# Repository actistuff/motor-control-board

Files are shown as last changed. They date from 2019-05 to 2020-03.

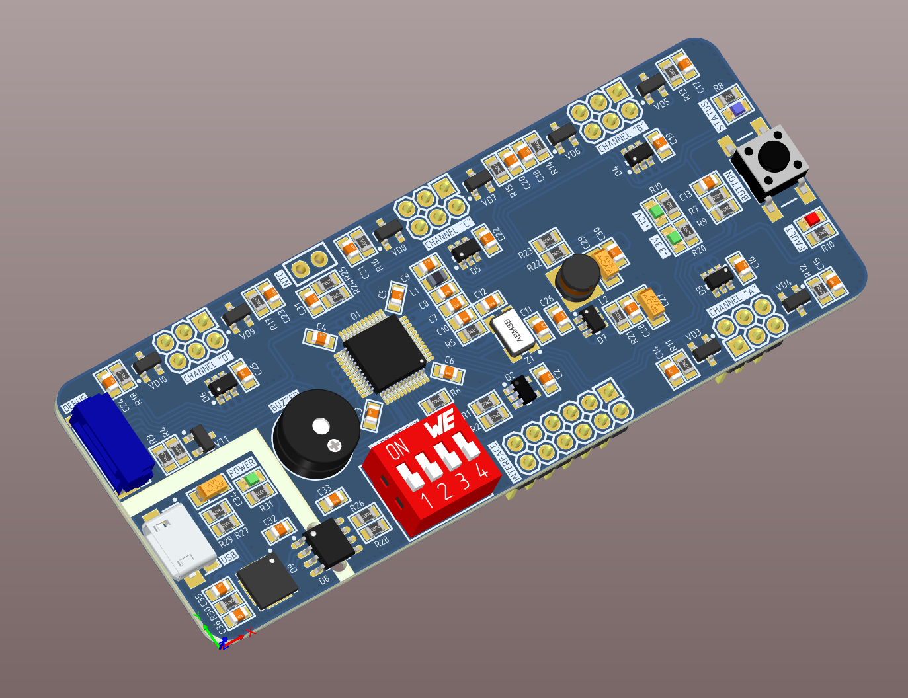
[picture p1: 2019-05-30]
Hardware/Mechanical/3D view. Part 1.PNG

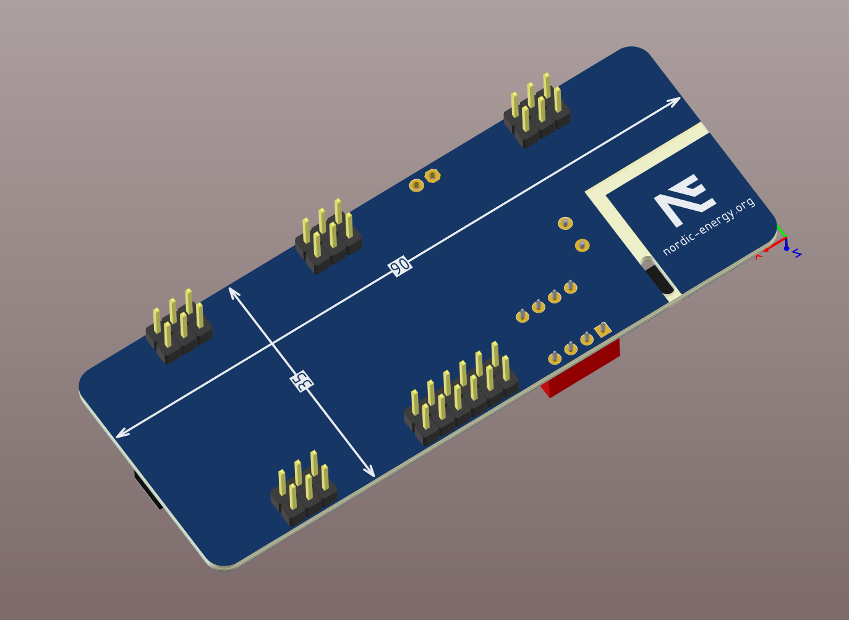
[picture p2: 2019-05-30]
Hardware/Mechanical/3D view. Part 2.PNG

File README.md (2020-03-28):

# Модуль управления силовым преобразователем

Проект создан для упрощения процесса разработки и создания прототипов силовых преобразователей энергии: инверторов напряжения, MPPT контроллеров, сварочных истоников тока, корректоров коэффициента мощности и т.д. Основой проекта является аппаратный модуль на базе специализированного (motor control) микроконтроллера STM32F334C8T6, адаптированный под прототипирование различных топологий преобразователей энергии. 

Плата управления

Особенно полезен модуль *MotorControlBoard* будет тем, кто только начинает изучать силовую электронику, так как его применение в процессе прототипирования позволит вам избавиться от большинства аппаратных проблем и упростить устройство. Важной частью проекта является наличие примеров *(Example)* кода для базовых топологий преобразователей и элементов системы управления.

# Технические характеристики

* Микроконтроллер: *STM32F334C8T6*
* Ядро контроллера: *Cortex-M4*
* Частота: *72 МГц*
* Наличие HRPWM: *да*
* Наличие FPU: *да*
* Внешняя EEPROM: *2 Кбит*
* Количество каналов: *4 полумоста*
* Напряжение питания: *5...18В*
* Ток потребления: *не более 0.07А*
* Температурный диапазон: *-20...+85°С*

# Структура проекта

* Firmware
    * Documents
    * Examples
    * Library

>

* Hardware
    * Documents
    * Manufacture
    * AltiumProject
    * Mechanical

# Назначение выводов

Модуль содержит 4 канала для управления полумостом, каждый из которых выведен на разъем PLS-6 и содержит в себе 2 канала HRPWM, 2 канала АЦП, вход сигнала ошибки и землю. Так же имеется основной вход для подачи питания, сигналов синхронизации и дополнительные I/O с программируемым функционалом.

Pinout

# Используемые инструменты

* [Altium Designer](https://www.altium.com/altium-designer/ "Официальный сайт CAD")
* [Visual Studio 2019](https://visualstudio.microsoft.com/ru/vs/ "Официальный сайт IDE")
* [VisualGDB](https://visualgdb.com/download/ "Официальный сайт плагина")
* [PVS-Studio](https://www.viva64.com/ru/pvs-studio/ "Официальный сайт")

# Лицензирование

Все исходные материалы для проекта распространяются по лицензии [MIT](./LICENSE "Описание лицензии"). Вы можете использовать проект в любом виде, в том числе и для коммерческой деятельности, но стоит помнить, что автор проекта не дает никаких гарантий на работоспособность устройства или частей проекта, а так же не несет никакой ответственности по искам или за нанесенный ущерб.

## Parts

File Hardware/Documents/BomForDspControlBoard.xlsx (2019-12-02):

Designator | Value | PartNumber | Manufacturer | Quantity | Comment | HelpURL
C1, C16, C17 | 1μF | CL10B105KO8NNNC | Samsung | 3 | Ceramic capacitor, 1μF, X7R, ±10%, 16V, 0603, -55...+125°C | https://www.digikey.com/product-detail/en/samsung-electro-mechanics/CL10B105KO8NNNC/1276-1019-1-ND/3889105
C2, C3, C4, C5, C6, C7, C8, C9, C34, C35, C39 | 10μF | CL10B106MQ8NRNC | Samsung | 11 | Ceramic capacitor, 10μF, X7R, ±10%, 6.3V, 0603, -55...+125°C | https://www.digikey.com/product-detail/en/samsung-electro-mechanics/CL10B106MQ8NRNC/1276-1948-1-ND/3890034
C10, C11, C12, C18, C21, C30, C31, C32, C33, C36, C40 | 0.1μF | CL10B104KB8NNNC | Samsung | 11 | Ceramic capacitor, 0.1μF, X7R, ±10%, 50V, 0603, -55...+125°C | https://www.digikey.com/product-detail/en/samsung-electro-mechanics/CL10B104KB8NNNC/1276-1000-1-ND/3889086
C15, C22, C23, C24, C25, C26, C27, C28, C29 | 0.01μF | CL10B103KB8NNNC | Samsung | 9 | Ceramic capacitor, 0.01μF, X7R, ±10%, 50V, 0603, -55...+125°C | https://www.digikey.com/product-detail/en/samsung-electro-mechanics/CL10B103KB8NNNC/1276-1009-1-ND/3889095
C19, C20 | 12pF | CL10C120JB8NNNC | Samsung | 2 | Ceramic capacitor, 12pF, NPO, ±10%, 50V, 0603, -55...+125°C | https://www.digikey.com/product-detail/en/samsung-electro-mechanics/CL10C120JB8NNNC/1276-1254-1-ND/3889340
C37 | 2.7pF | CL10C2R7BB8NNNC | Samsung | 1 | Ceramic capacitor, 2.7pF, NPO, ±10%, 50V, 0603, -55...+125°C | https://www.digikey.com/product-detail/en/samsung-electro-mechanics/CL10C2R7BB8NNNC/1276-1240-1-ND/3889326
C38 | 4.7pF | CL10C4R7CB8NNNC | Samsung | 1 | Ceramic capacitor, 4.7pF, NPO, ±10%, 50V, 0603, -55...+125°C | https://www.digikey.com/product-detail/en/samsung-electro-mechanics/CL10C4R7CB8NNNC/1276-1282-1-ND/3889368
D1 |  | TCAN334DCNR | Texas Instruments | 1 | IC CAN transceiver, 1Mbps, Half-duplex, 3...3.6V, -40...+125°C, SOT23-8 | https://www.digikey.com/product-detail/en/texas-instruments/TCAN334DCNR/296-47830-1-ND/8133179
D2, D3 |  | AP3429AKTTR-G1 | Diodes Incorporated | 2 | DC/DC buck converter, input 2.7...5.5V, 1MHz, output 0.6...5V, 2A, -40...+85°C, SOT23-6 | https://www.digikey.com/product-detail/en/diodes-incorporated/AP3429AKTTR-G1/AP3429AKTTR-G1DICT-ND/5359842
D4 |  | TLV70033DDCR | Texas Instruments | 1 | Linear voltage regulator, input 5.5V, 0.25V, output 3.3V, 200 mA, -40...+85°C, SOT-23-5 | https://www.digikey.com/product-detail/en/texas-instruments/TLV70033DDCR/296-27937-1-ND/2440840
D5 |  | STM32F334C8T6 | STMicroelectronics | 1 | IC microcontroller, 32-Bit, Cortex-M4, 72MHz, 64KB, 12KB, 2...3.6V, -40...+85°C, 48-LQFP | https://www.digikey.com/products/en?keywords=STM32F334C8T6
D6, D8, D9, D11, D12, D13, D14 |  | SN74LVC2G17DCKR | Texas Instruments | 7 | IC logic buffer, 1.65...5.5V, -40...+125°C, SC-70-6 | https://www.digikey.com/product-detail/en/texas-instruments/SN74LVC2G17DCKR/296-13013-1-ND/479736
D7 |  | 24AA01T-I/OT | Microchip Technology | 1 | IC memory, EEPROM, 1KB (128x8), 400 kHz, I2C, 1.7...5.5V, -40...+85°C, SOT-23-5 | https://www.digikey.com/product-detail/en/microchip-technology/24AA01T-I-OT/24AA01T-I-OTCT-ND/857670
D10 |  | 5M80ZE64I5N | Intel | 1 | IC CPLD logic, MAX V, 100MHz, 80LE, 1.71...1.89V, -40...+100°C, 64-EQFP | https://www.digikey.com/product-detail/en/intel/5M80ZE64I5N/544-2817-ND/2660734
D15 |  | ESP32-PICO-D4 | Espressif Systems | 1 | IC RF transceiver, 802.11b/g/n + Bluetooth v4.2, 2.4GHz, 32-Bit, Xtensa LX6, 4Mb, 520KB, 2.7...3.6V, -40...+85°C, 48-LGA | https://www.digikey.com/product-detail/en/espressif-systems/ESP32-PICO-D4/1904-1029-1-ND/9381738
L1, L2 | 4.7μH | SRP2510A-4R7M | Bourns | 2 | Fixed inductor, 4.7μH, ±20%, SRP2510A, 1.36A, -40...+125°C | https://www.digikey.com/product-detail/en/bourns-inc/SRP2510A-4R7M/SRP2510A-4R7MCT-ND/7354840
L3 | 10μH | LQM18FN100M00D | Murata Electronics | 1 | Fixed inductor, 10μH, ±20%, 0603, 50mA, -55...+125°C | https://www.digikey.com/product-detail/en/murata-electronics-north-america/LQM18FN100M00D/490-4025-1-ND/1016285
L4 | 1.6nH | CW161009A-1N6D | Bourns | 1 | Fixed inductor, 1.6nH, ±20%, 0603, 700mA, -40...+125°C | https://www.digikey.com/product-detail/en/bourns-inc/CW161009A-1N6D/CW161009A-1N6DCT-ND/9826842
R1 | 120R | RC0603JR-07120RL | Yageo | 1 | Resistor film, 120R, ±5%, 0603, 0.1W, -55...+125°C | https://www.digikey.com/product-detail/en/yageo/RC0603JR-07120RL/311-120GRCT-ND/729653
R2, R4 | 10k | RC0603FR-0710KL | Yageo | 2 | Resistor film, 10k, ±1%, 0603, 0.1W, -55...+125°C | https://www.digikey.com/product-detail/en/yageo/RC0603FR-0710KL/311-10.0KHRCT-ND/729827
R3 | 2k2 | RC0603FR-072K2L | Yageo | 1 | Resistor film, 2k2, ±1%, 0603, 0.1W, -55...+125°C | https://www.digikey.com/product-detail/en/yageo/RC0603FR-072K2L/311-2.20KHRCT-ND/729963
R5 | 4k99 | RC0603FR-074K99L | Yageo | 1 | Resistor film, 4k99, ±1%, 0603, 0.1W, -55...+125°C | https://www.digikey.com/product-detail/en/yageo/RC0603FR-074K99L/311-4.99KHRCT-ND/730166
R6, R7, R35, R36, R38 | 10k | RC0603JR-0710KL | Yageo | 5 | Resistor film, 10k, ±5%, 0603, 0.1W, -55...+125°C | https://www.digikey.com/product-detail/en/yageo/RC0603JR-0710KL/311-10KGRCT-ND/729647
R8, R9, R12, R13, R14, R15, R16, R17, R18, R19, R20, R21, R22, R23, R24, R25, R26, R27, R28, R29, R30, R31, R32, R33, R34 | 100R | RC0603JR-07100RL | Yageo | 25 | Resistor film, 100R, ±5%, 0603, 0.1W, -55...+125°C | https://www.digikey.com/product-detail/en/yageo/RC0603JR-07100RL/311-100GRCT-ND/729644
R10, R11 | 4k7 | RC0603JR-074K7L | Yageo | 2 | Resistor film, 4k7, ±5%, 0603, 0.1W, -55...+125°C | https://www.digikey.com/product-detail/en/yageo/RC0603JR-074K7L/311-4.7KGRCT-ND/729732
R37 | 1k | RC0603JR-071KL | Yageo | 1 | Resistor film, 1k, ±5%, 0603, 0.1W, -55...+125°C | https://www.digikey.com/product-detail/en/yageo/RC0603JR-071KL/311-1.0KGRCT-ND/729624
VD1 |  | ESDCAN03-2BWY | Texas Instruments | 1 | Zener diode, 24V, 250W, 3A peak, 3pF, SC-70, -55...+175°C | https://www.digikey.com/product-detail/en/stmicroelectronics/ESDCAN03-2BWY/497-15846-1-ND/5305256
VD2 |  | 150060VS75000 | Wurth | 1 | LED, Green, 20mA, 2V, 0603, -55...+150°C | https://www.digikey.com/product-detail/en/wurth-electronics-inc/150060VS75000/732-4980-1-ND/4489904
VD3 |  | 150060YS75000 | Wurth | 1 | LED, Yellow, 20mA, 2V, 0603, -55...+150°C | https://www.digikey.com/product-detail/en/wurth-electronics-inc/150060YS75000/732-4981-1-ND/4489907
VD4 |  | 150060RS55040 | Wurth | 1 | LED, Red, 20mA, 2V, 0603, -55...+150°C | https://www.digikey.com/product-detail/en/w-rth-elektronik/150060RS55040/732-12015-1-ND/8557225
VD5, VD6, VD7, VD8, VD9, VD10, VD11, VD12 |  | BAV199WQ-7 | Diodes Incorporated | 8 | Diode array, 85V, 140mA, 1.1V, 3us, SC-70, -65...+150°C | https://www.digikey.com/product-detail/en/diodes-incorporated/BAV199WQ-7/BAV199WQ-7DICT-ND/6003950
X1 |  | PLS-30 | Connfly | 1 | Connector, 30pin, 2.54mm, 500VAC, 3A | https://www.chipdip.ru/product/pls-40r-2
X2 |  | PBD-4 | Connfly | 1 | Connector, 4pin, 2.54mm, 500VAC, 3A | https://www.chipdip.ru/product/pbd-4
X3 |  | SM04B-GHS | JST | 1 | Connector, 4pin, 1.25mm, 50VDC, 1A | https://www.digikey.com/product-detail/en/jst-sales-america-inc/SM04B-GHS-TB-LF-SN/455-1566-1-ND/807834
X4 |  | SM06B-GHS | JST | 1 | Connector, 6pin, 1.25mm, 50VDC, 1A | https://www.digikey.com/product-detail/en/jst-sales-america-inc/SM06B-GHS-TB-LF-SN/455-1568-1-ND/807836
X5 |  | U.FL-R-SMT(01) | Hirose Electric | 1 | Connector u.FL, 50 Ohm, 6GHz | https://www.digikey.com/product-detail/en/hirose-electric-co-ltd/U.FL-R-SMT-01/H9161-ND/513010
Z1 |  | FL0800008Q | Diodes Incorporated | 1 | Crystal, 8MHz, 12pF, ±30ppm, case 3225, -40...+85°C | https://www.digikey.com/product-detail/en/diodes-incorporated/FL0800008Q/FL0800008QDICT-ND/9952912

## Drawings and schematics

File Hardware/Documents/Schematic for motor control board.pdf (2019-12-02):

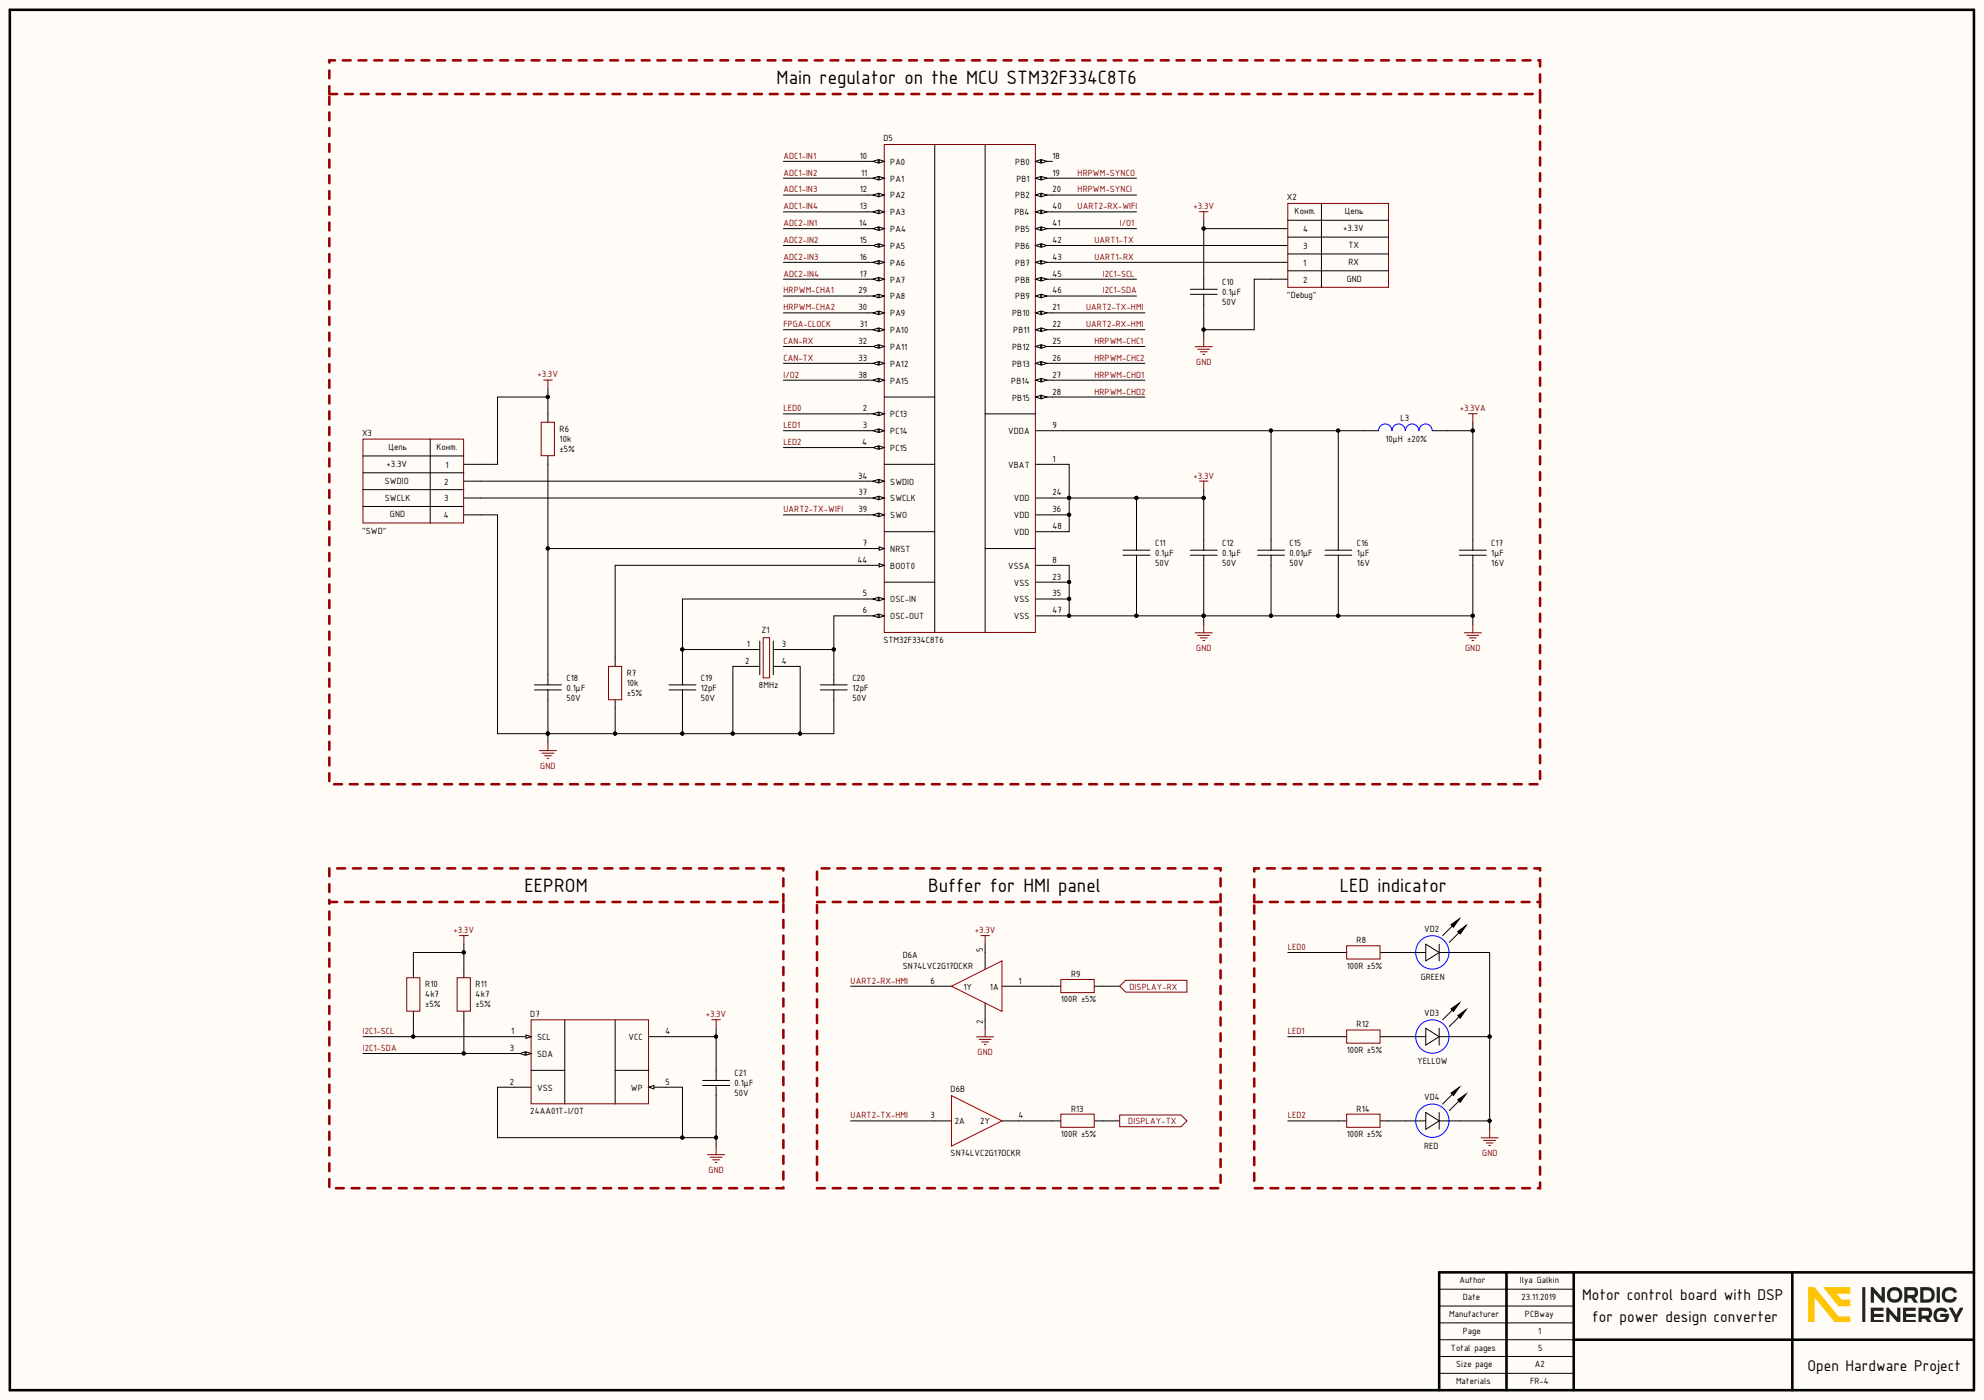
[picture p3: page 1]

Main regulator on the MCU STM32F334C8T6

Конт. | Цепь

2 | GND

Цепь | Конт.

SWDIO | 2

SWCLK | 3

GND | 4

Author | Ilya Galkin | Motor control board with DSP for power design converter

Date | 23.11.2019

Manufacturer | PCBway

Page

Total pages | | | Open Hardware Project

Size page | A2

Materials | FR-4

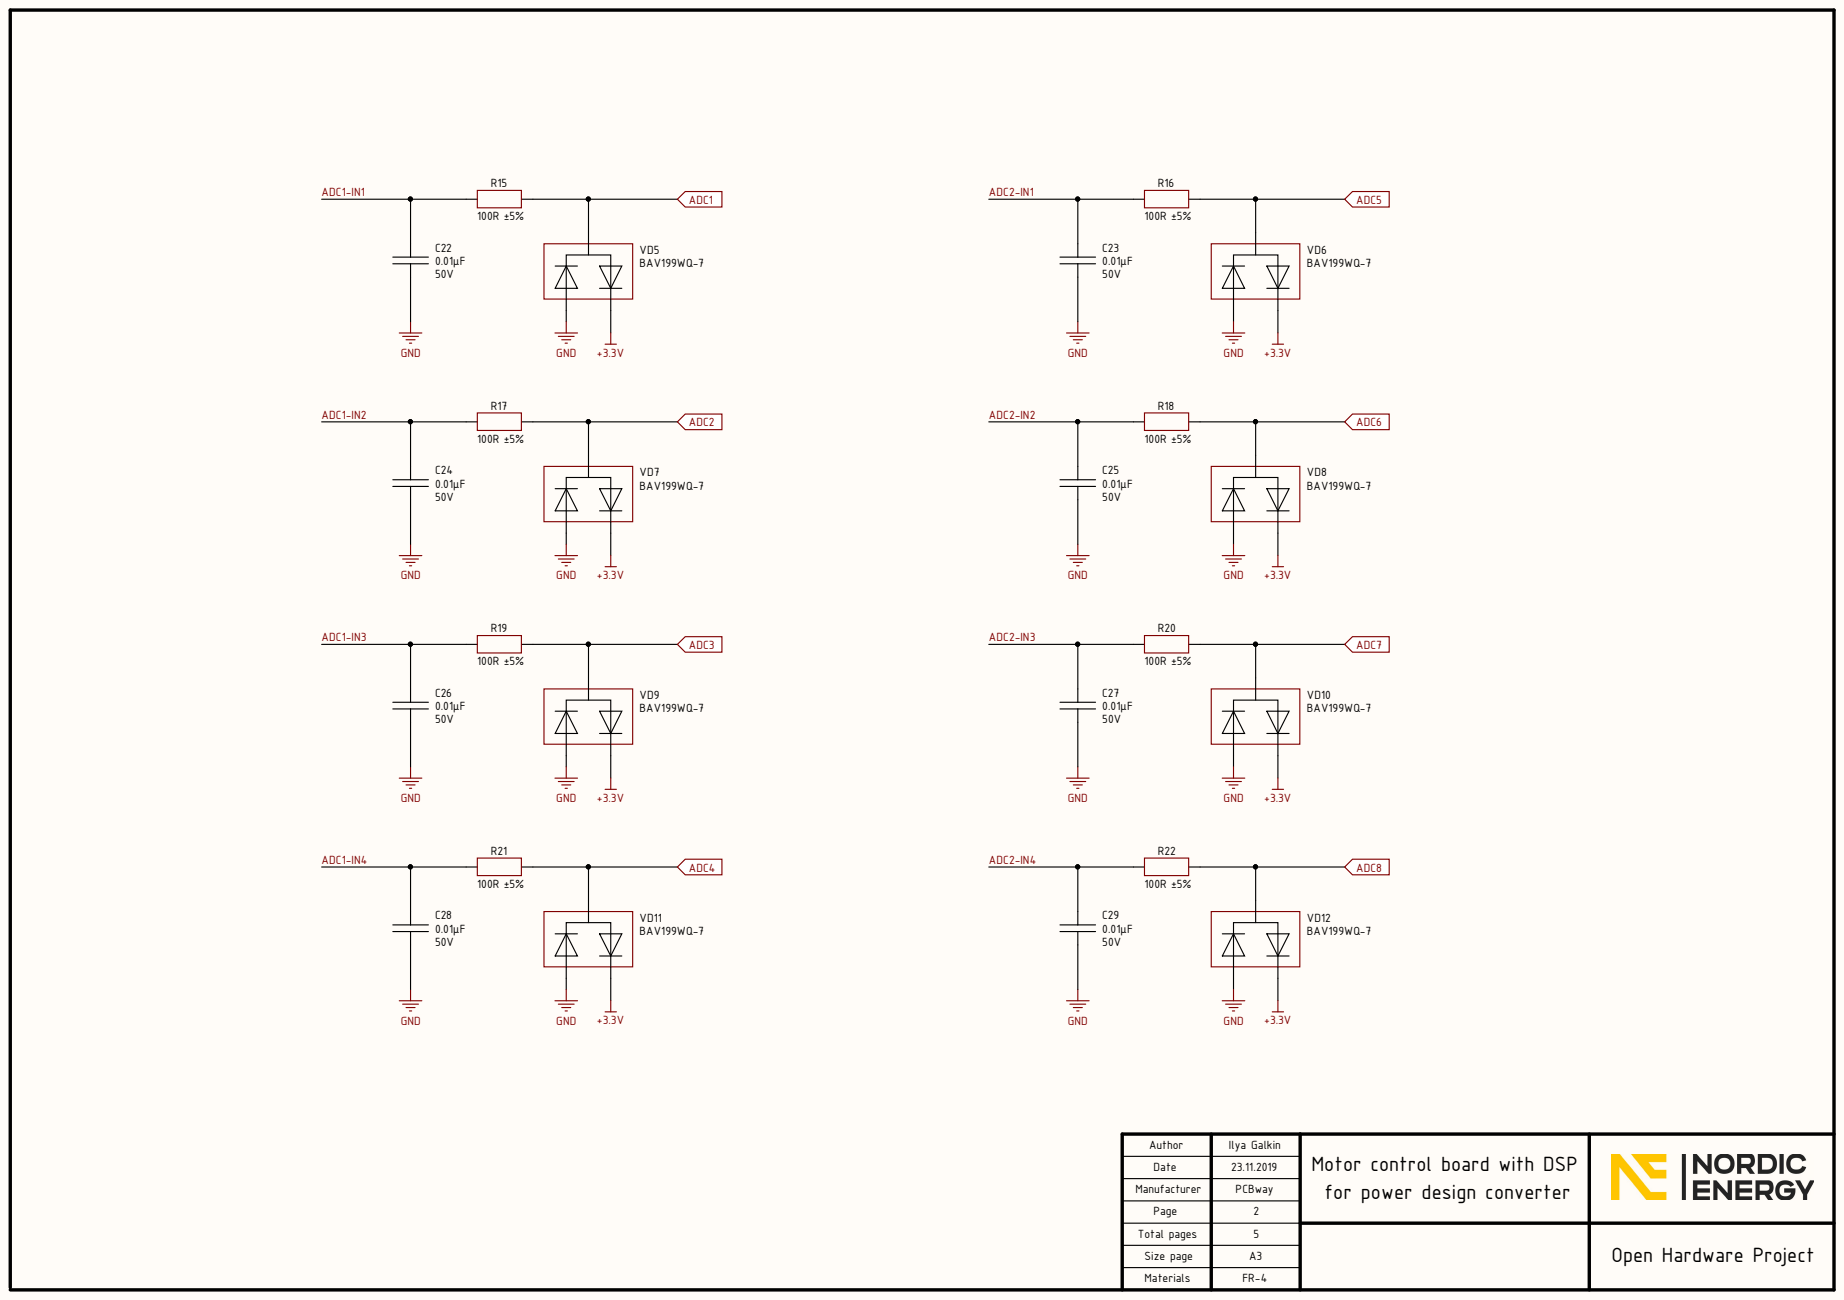
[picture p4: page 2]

Author | Ilya Galkin | Motor control board with DSP for power design converter

Date | 23.11.2019

Manufacturer | PCBway

Page

Total pages

Size page | A3

Materials

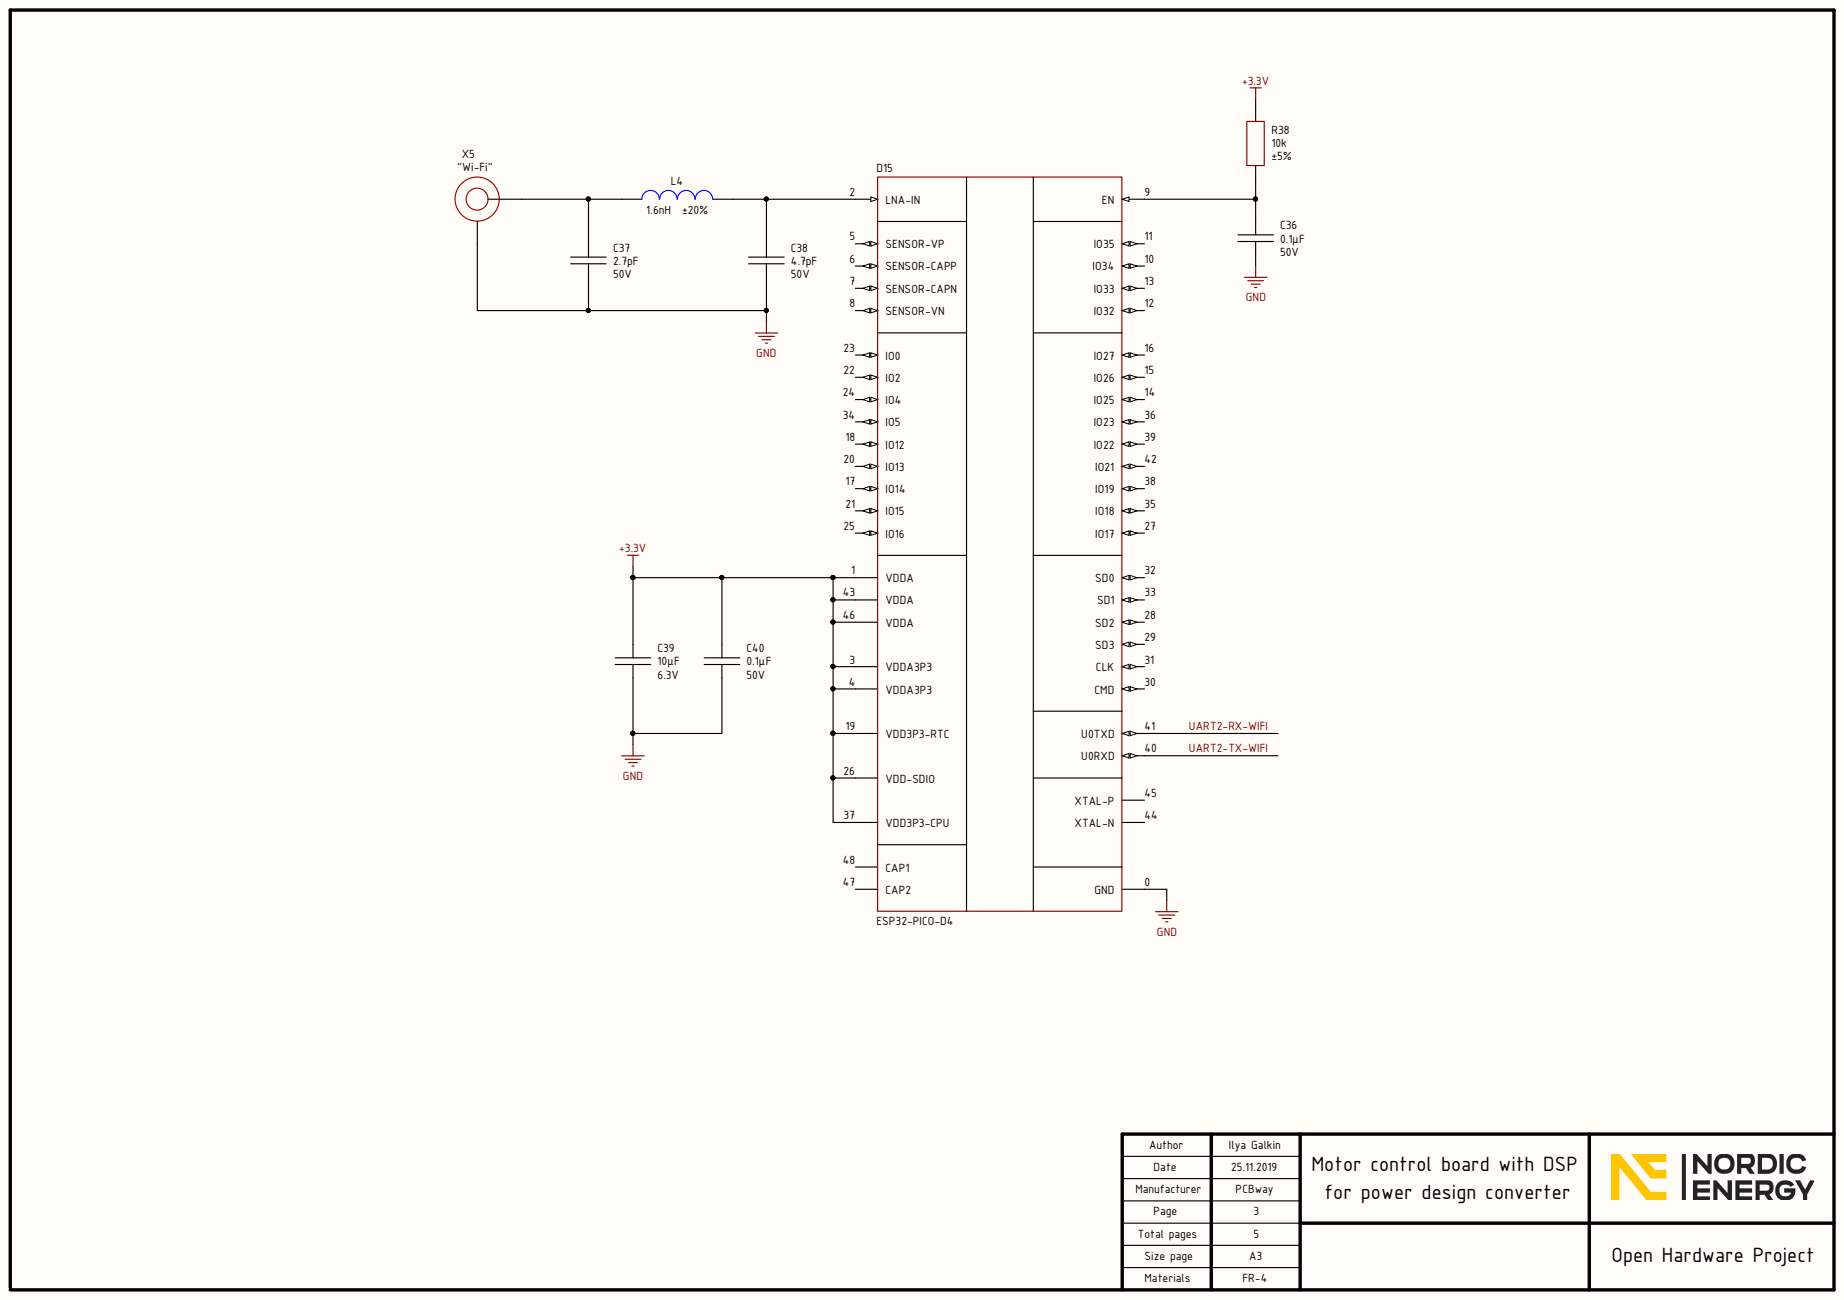
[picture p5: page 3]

VDDA 43

VDDA 46

VDDA3P3 3

VDDA3P3 4

VDD3P3-RTC 19

VDD-SDIO 26

Author | Ilya Galkin | Motor control board with DSP for power design converter

Date | 25.11.2019

Manufacturer | PCBway

Page

Total pages

Size page | A3

Materials

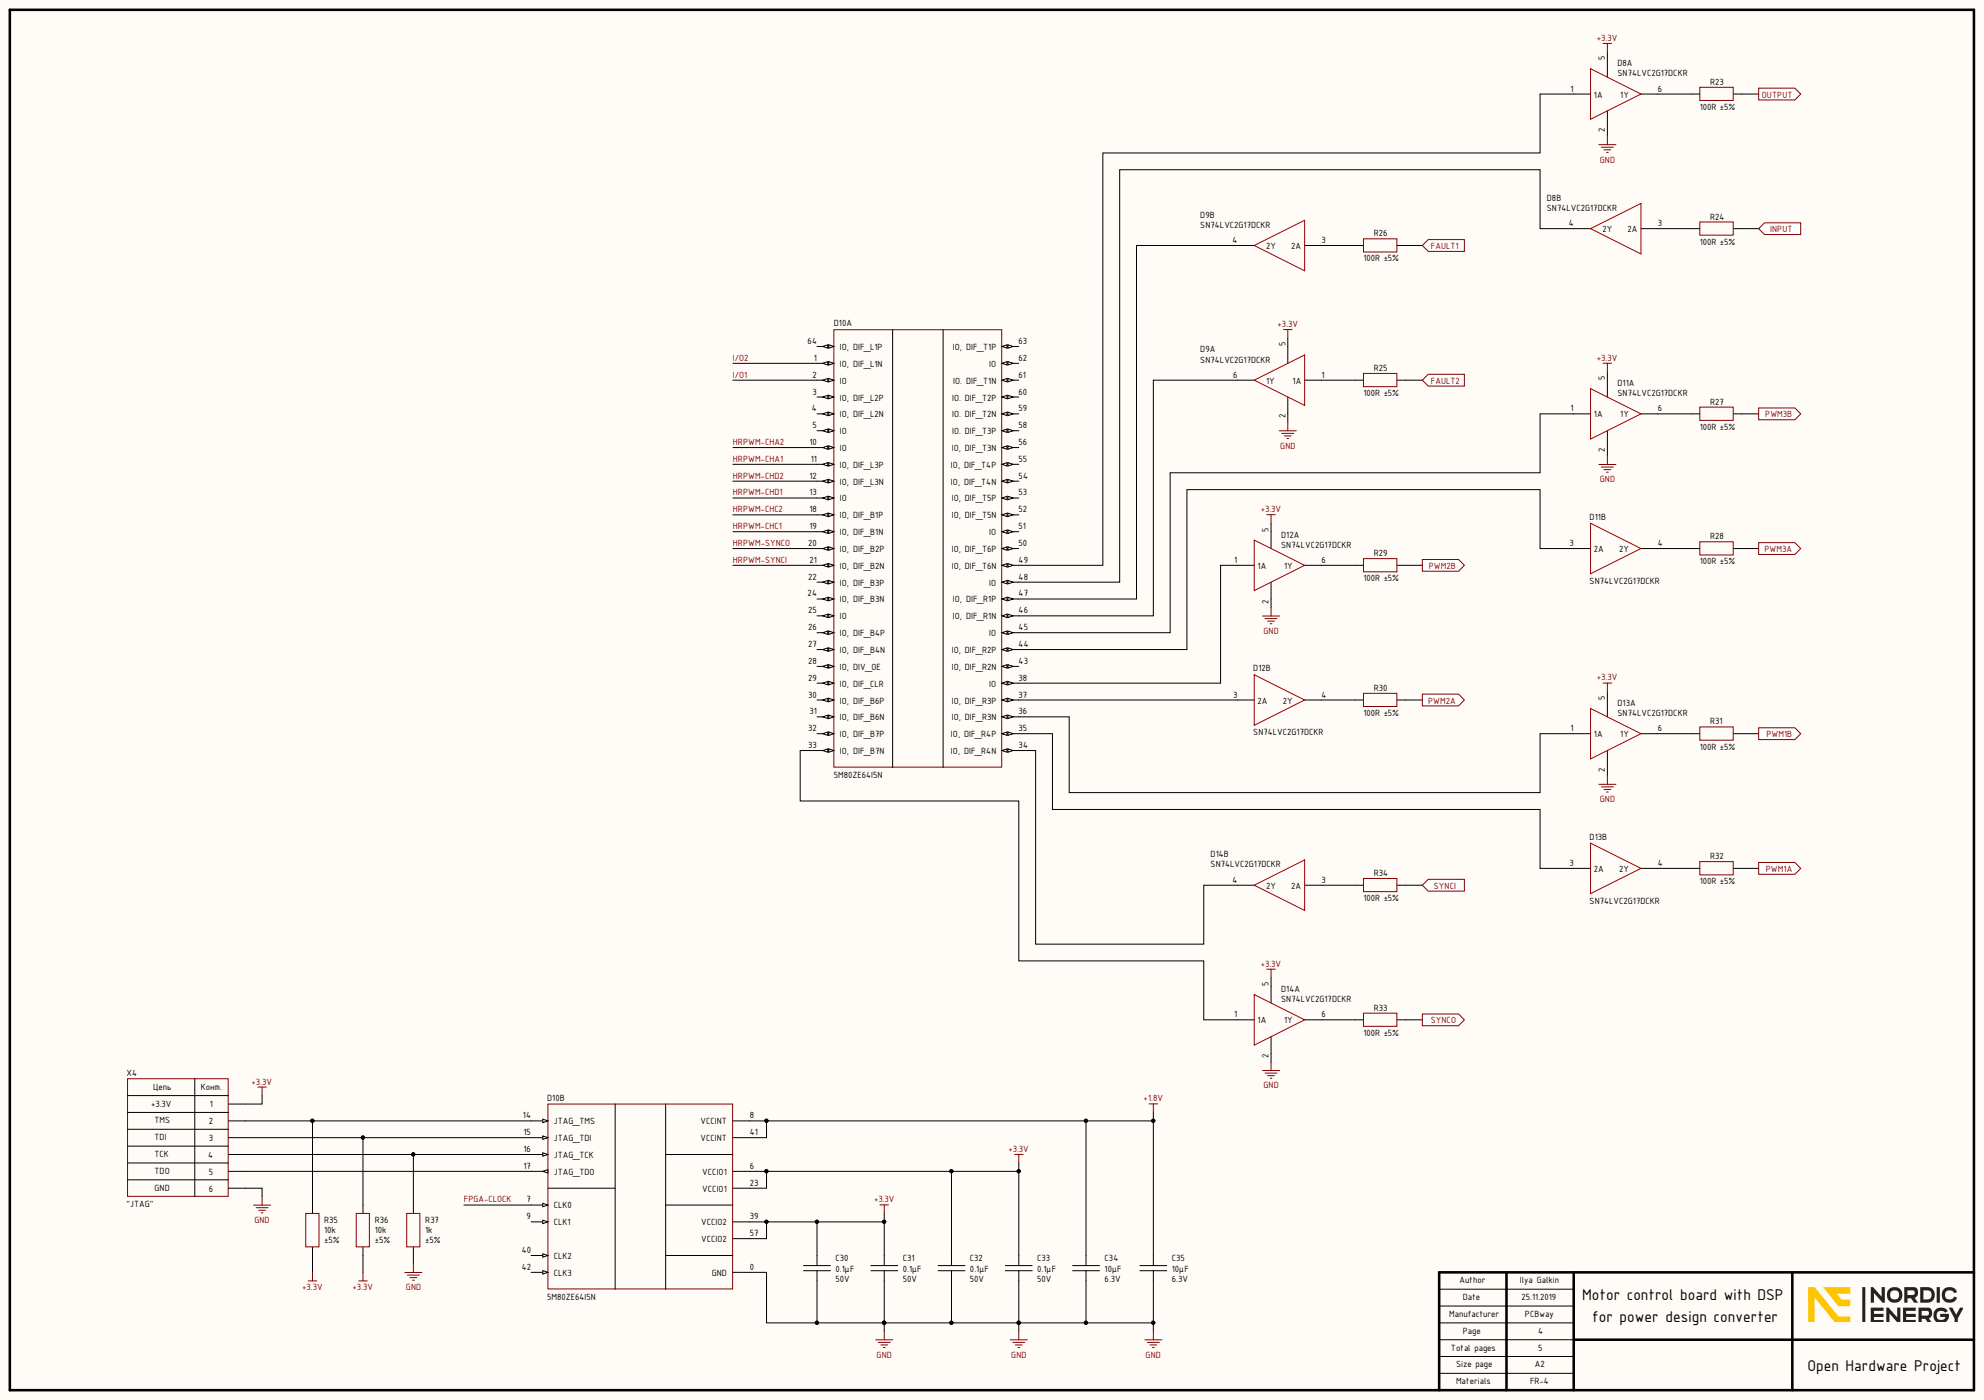
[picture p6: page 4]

Цепь | Конт .
+3.3V TMS TDI TCK TDO GND

JTAG_TCK 16 | 6

Motor control board with DSP
for power design converter

Manufacturer Page Total pages

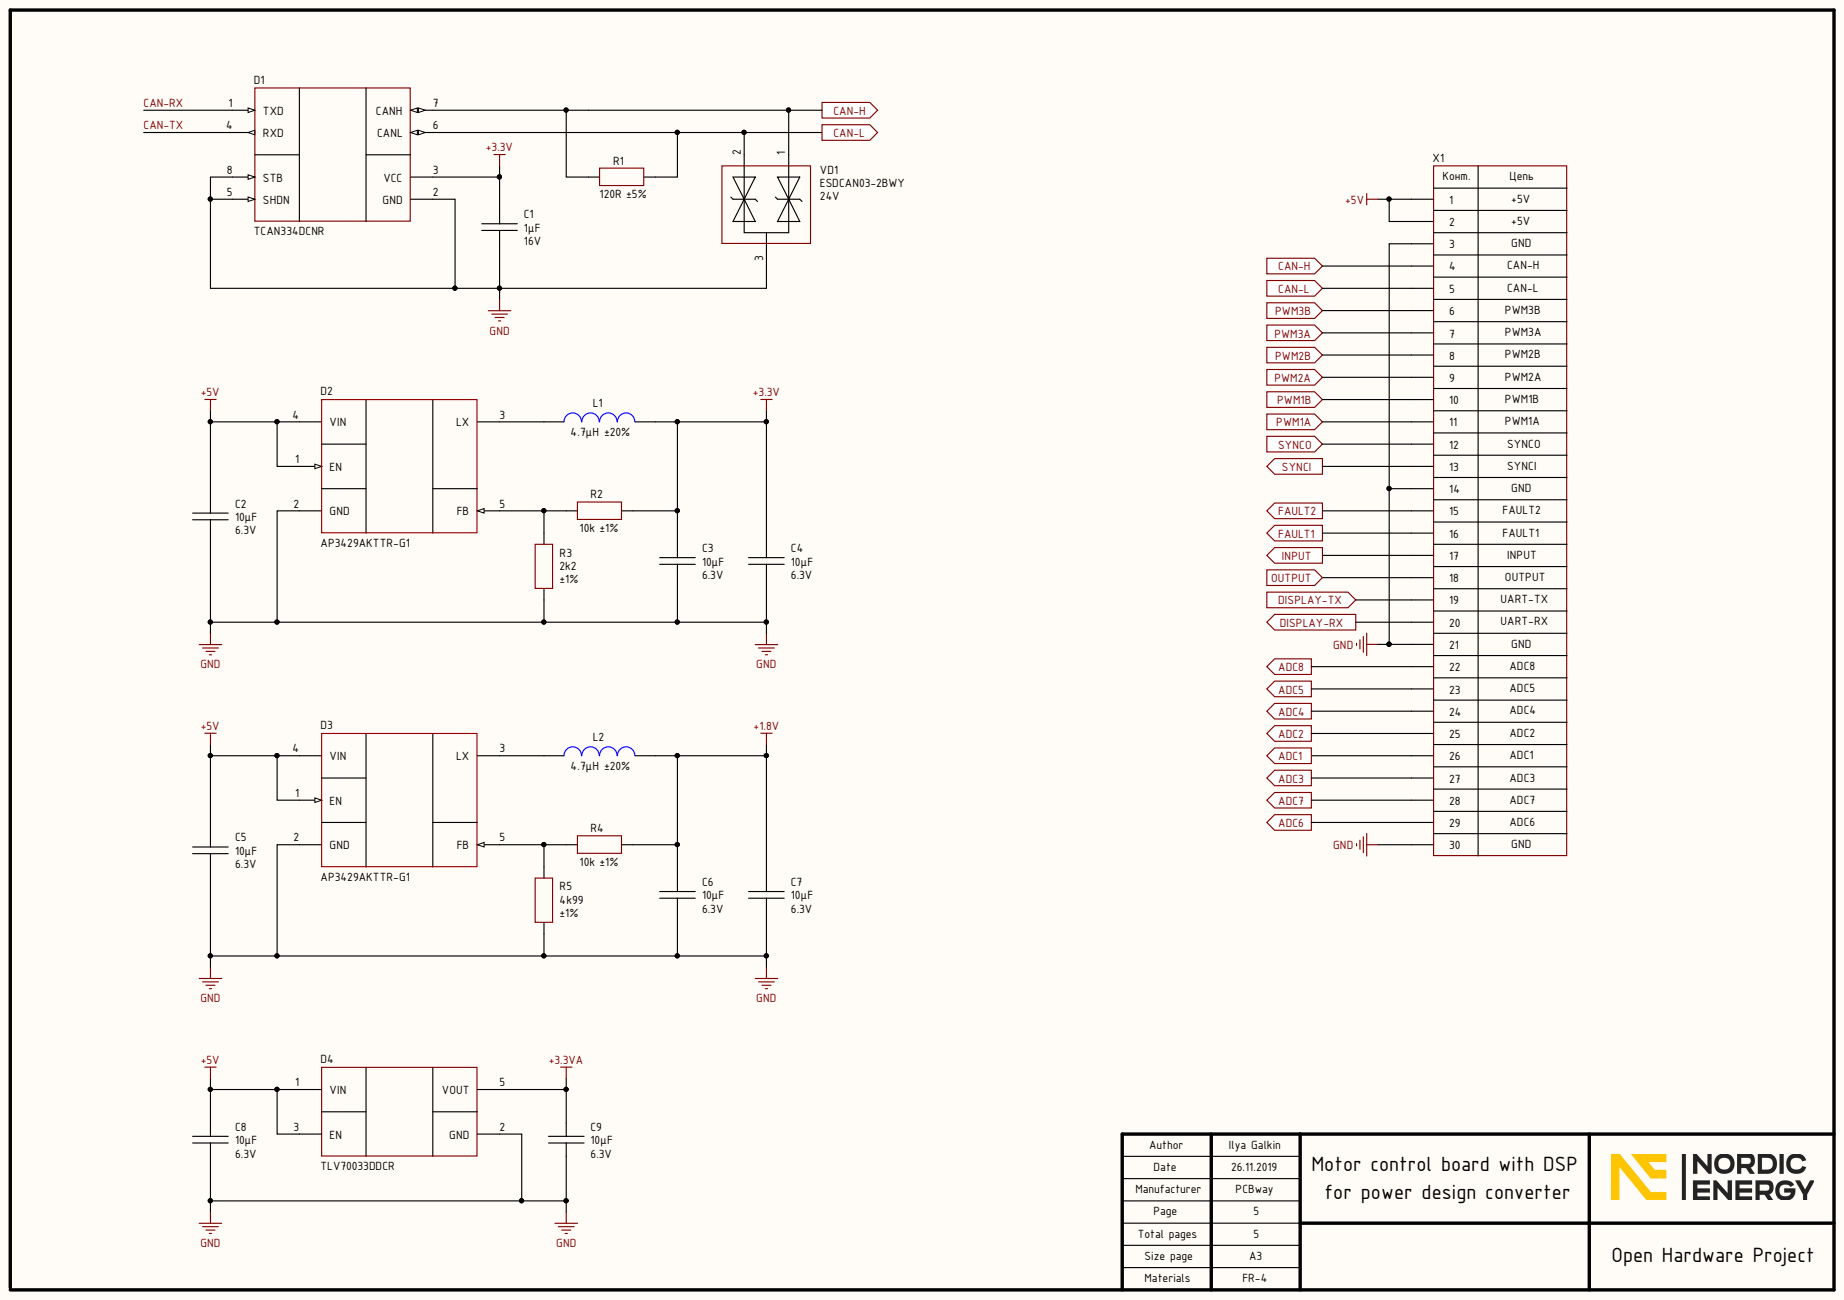
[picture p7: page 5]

TXD RXD | CAN H CAN L

S T B S H D N | VCC G N D | 3 | R 1

Конт . | Цепь

3456789 | CAN-L

G N D
PWM1A PWM1B PWM2A PWM2B PWM3A PWM3B

CAN-H

LX | 3 VIN

12 | SYNCI SYNCO

19 | UAR T-T X

20 | UAR T-R X

22 | ADC8

23 | ADC5

24 | ADC4

25 | ADC2

26 | ADC1

27 | ADC3

28 | ADC7

29 | ADC6

Author Date | Ilya Galki n | Motor control board with DSP for power design converter

Manufacturer Page Total pages

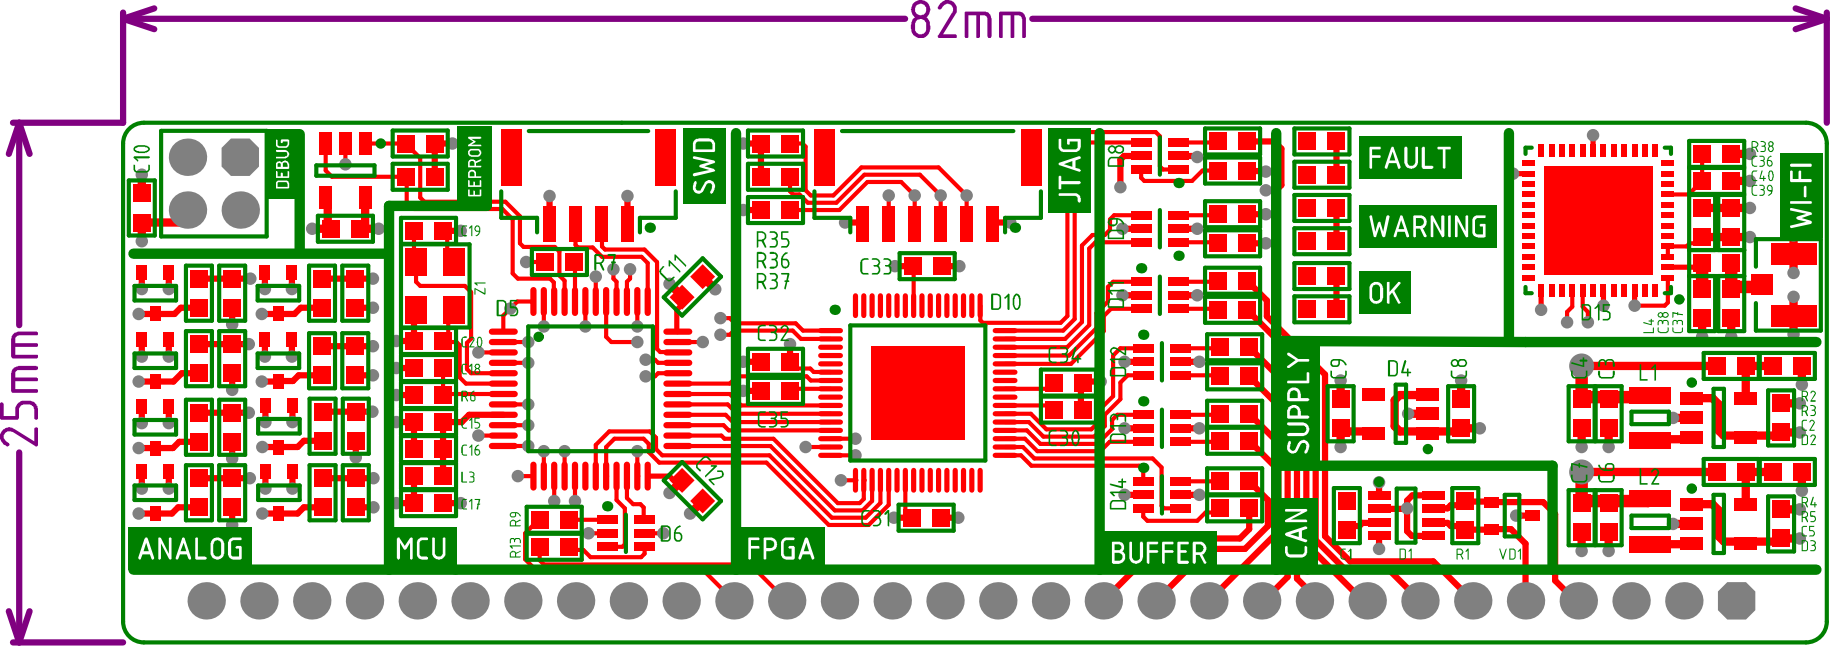
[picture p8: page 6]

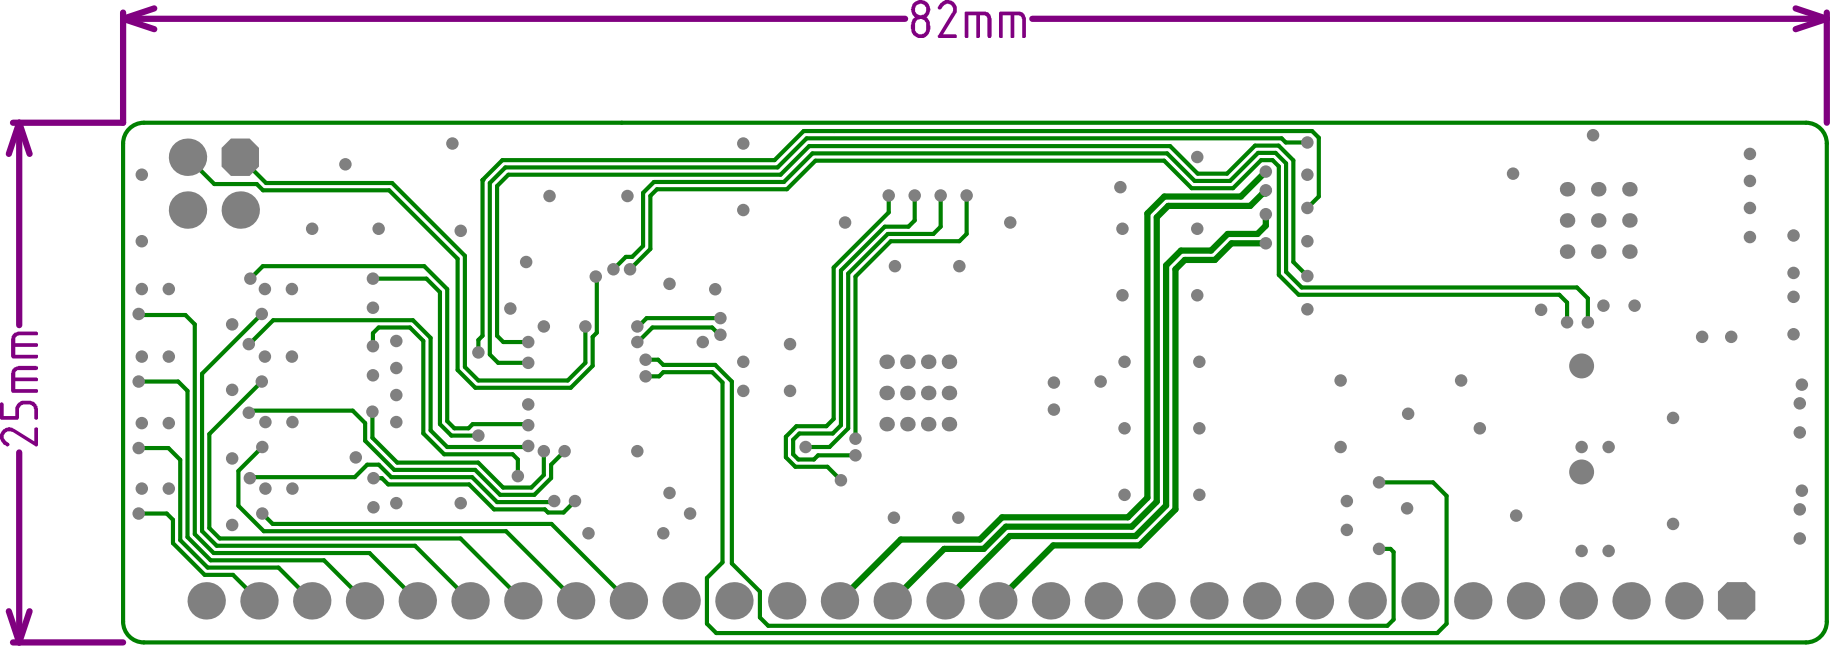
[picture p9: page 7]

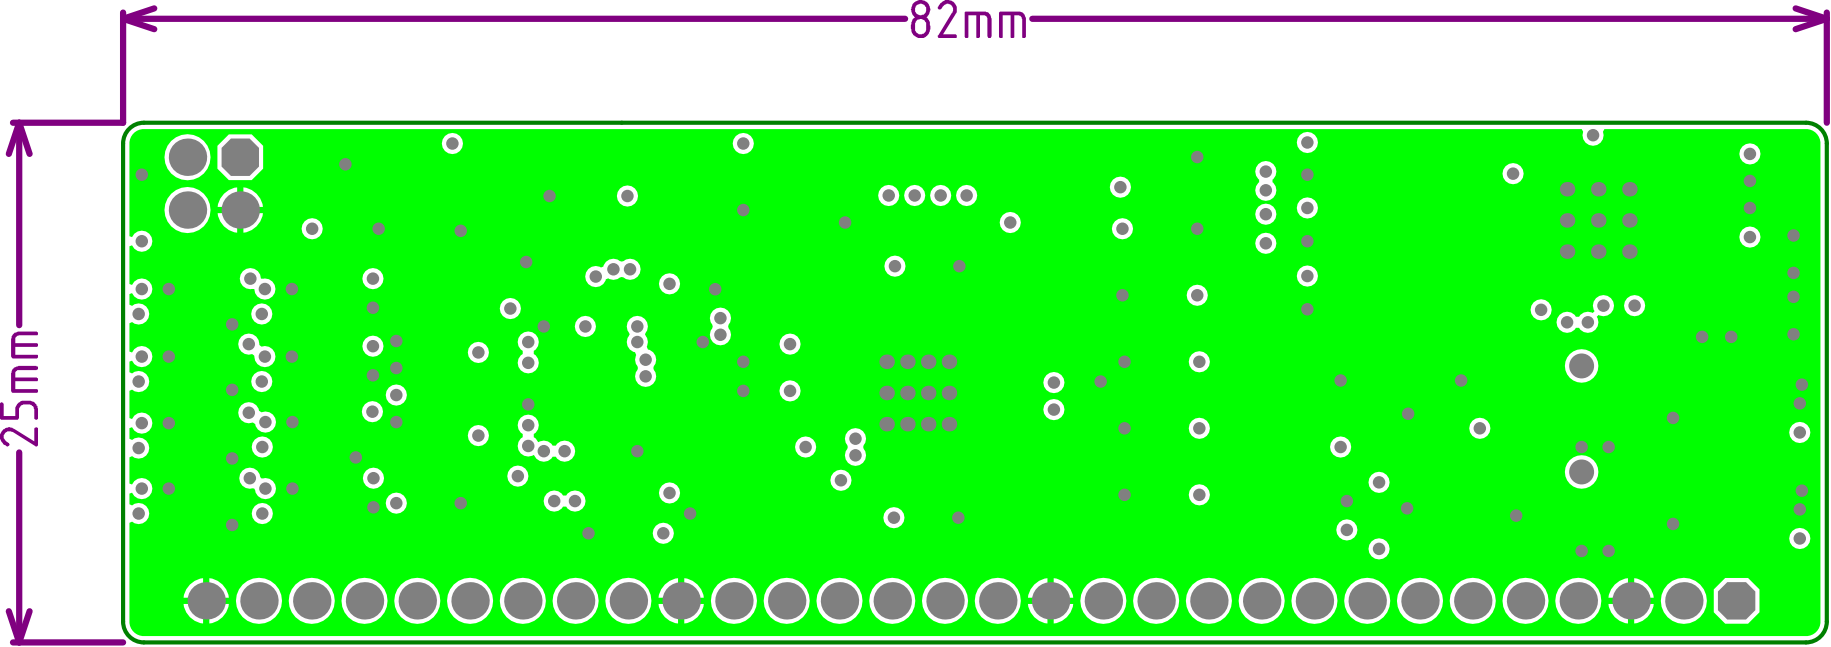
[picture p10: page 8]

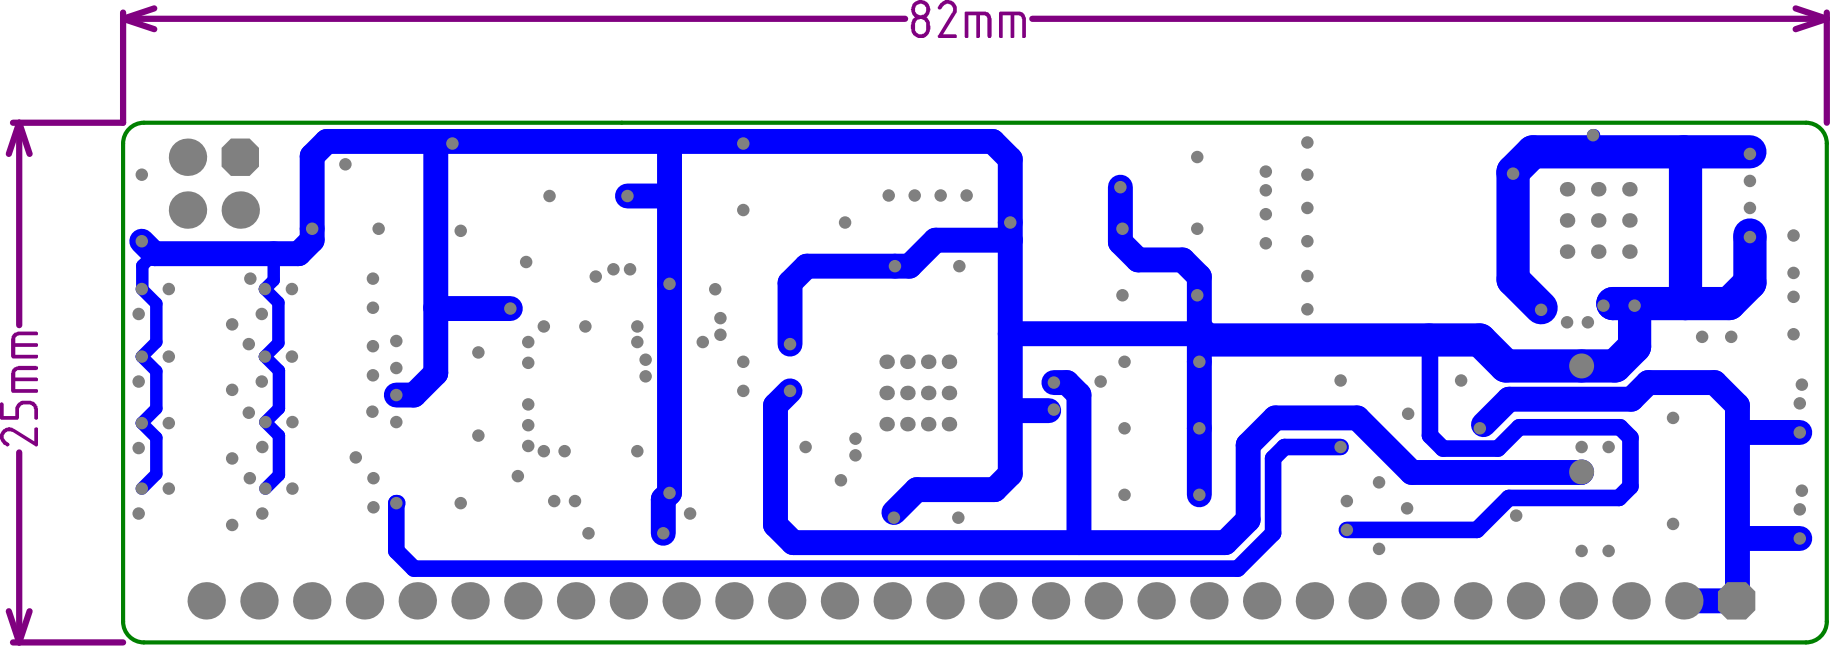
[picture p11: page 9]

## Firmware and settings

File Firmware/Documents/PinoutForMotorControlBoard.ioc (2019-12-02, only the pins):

Mcu.UserName=STM32F334C8Tx
PA0.Signal=ADC1_IN1
PA1.Signal=ADC1_IN2
PA10.GPIO_Label=FPGA-CLOCK
PA10.Signal=HRTIM1_CHB1
PA11.Signal=CAN_RX
PA12.Signal=CAN_TX
PA13.Signal=SYS_JTMS-SWDIO
PA14.Signal=SYS_JTCK-SWCLK
PA15.GPIO_Label=I/O2
PA15.Signal=GPIO_Output
PA2.Signal=ADC1_IN3
PA3.Signal=ADC1_IN4
PA4.Signal=ADC2_IN1
PA5.Signal=ADC2_IN2
PA6.Signal=ADC2_IN3
PA7.Signal=ADC2_IN4
PA8.Signal=HRTIM1_CHA1
PA9.Signal=HRTIM1_CHA2
PB1.Signal=HRTIM1_SCOUT
PB10.GPIO_Label=UART3-TX-HMI
PB10.Signal=USART3_TX
PB11.GPIO_Label=UART3-RX-HMI
PB11.Signal=USART3_RX
PB12.Signal=HRTIM1_CHC1
PB13.Signal=HRTIM1_CHC2
PB14.Signal=HRTIM1_CHD1
PB15.Signal=HRTIM1_CHD2
PB2.Signal=HRTIM1_SCIN
PB3.GPIO_Label=UART2-TX-WIFI
PB3.Signal=USART2_TX
PB4.GPIO_Label=UART2-RX-WIFI
PB4.Signal=USART2_RX
PB5.GPIO_Label=I/O1
PB5.Signal=GPIO_Output
PB6.GPIO_Label=UART1-TX-DEBUG
PB6.Signal=USART1_TX
PB7.GPIO_Label=UART1-RX-DEBUG
PB7.Signal=USART1_RX
PB8.Signal=I2C1_SCL
PB9.Signal=I2C1_SDA
PC13.GPIO_Label=LED0
PC13.Signal=GPIO_Output

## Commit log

2019-05-30 git init
    [BOM for motor control board.xlsx, Main MCU. Page 1.SchDoc, Motor control board.PrjPcb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]
2019-08-10 docs: Добавил исключение файлов предпросмотра для AD
    [Main MCU. Page 1.SchDoc]
2019-11-22 new: Начал разработку 2-й ревизии. Завершил часть схемы
    - Завершил обвязку STM32F334C8T6: EEPROM, debug, uart для дисплея,
    система питания, защищенные i/o, LED-ы;
    - Добавил защиту портов АЦП и входные фильтры низкой частоты (ФНЧ).
    [ControllerDSP.SchDoc, Main MCU. Page 1.SchDoc, MotorControlBoard.PrjPcb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]
2019-11-24 new: Завершил схему части Wi-Fi модуля на базе ESP32-PICO-D4
    [ControllerDSP.SchDoc, MotorControlBoard.PrjPcb, WiFi.SchDoc]
2019-11-26 new: Завершил схему аппаратных защит на CPLD MAX V
    [WiFi.SchDoc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]
2019-11-28 new: Завершил принципиальную схему модуля управления
    [CanAndSupply.SchDoc, ControllerDSP.SchDoc, DspControlBoard.PrjPcb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]
2019-11-29 new: Завершил компоновку печатной платы и начал трассировку
    [CanAndSupply.SchDoc, ControllerDSP.SchDoc, ProtectionADC.SchDoc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]
2019-11-30 new: Завершил трассировку печатной платы, требуется ревью и экспорт КД
    [CanAndSupply.SchDoc, ControllerDSP.SchDoc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]
2019-12-02 new: Выполнил ревью печатной платы, внес мелкие правки в слой top assy
2019-12-02 docs: Сгенерировал документацию для производства
    - Gerber файлы и NC drill для изготовления печатных плат;
    - BOM (спецификация/список компонентов);
    - PDF с принципиальной схемой и дизайном платы.
    [BOM for motor control board.xlsx, BomForDspControlBoard.xlsx]
2019-12-02 docs: Добавил файл с pinout для контроллера STM32F334
2020-03-28 docs: Обновил информацию о проекте в readme
